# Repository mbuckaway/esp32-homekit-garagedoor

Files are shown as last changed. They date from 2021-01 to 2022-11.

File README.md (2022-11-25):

# ESP32 GarageDoor Controller for HomeKit

## What is it

ESP32 dedicated Garage Door controller. When Espressif, created their Homekit SDK for the ESP32, the time was ripe to move the garage door controller to a smaller platform. The ESP32 IDF and Homekit SDKs made incorporating homekit functionity into a sample platform easy.

For complete information on the project, please see the WIKI in the github repo: [WIKI](https://github.com/mbuckaway/esp32-homekit-garagedoor/wiki)

## How this Works

This device is based on the Espressif SDK and uses the open source version of the Espressif Homekit SDK. It uses my own network component. This network component uses BluFi to configure WIFI creds and control the device. You will need the Espressif EspBluFi app from the Apple Appstore.

The difference with this controller and others is it uses both a switch on the lower part of the door to sensor it's actually closed and a switch on the upper side of the door to sensor it's actually open. With only a close switch, one can only assume the garage door actually makes it all the way up to be open. The two switches allow us to add a motion sensor service to sensor when the door is in motion. I use that to turn the garage light automatically on when the door moves.

The code configures the following services that make up the garage door accessory:

- Garage Door
- Close Sensor
- Open Sensor
- Motion Sensor (sense when the door is in motion)
- Switch to force the door to move (used for automations to override security "issues")
- Switch to close the door when it is open (and only open). Homekit sometimes loses the door status and this control is required for automation to work reliably.

What is missing from this unit is the obstruction detection. At some point, I may add a eye beam to detect something is in the way, but the old garage door already has that as a safety features, so having your phone notify you of the obstruction seems moot.

The code uses a button library to monitor the door switches and automatically debounces the switches. Additionally, the routine the monitors the open and close switches updates Homekit with the changes in status, so the home app almost instantly. However, Homekit seems to have a bug in it where if you control the door without using the Home App, it loses track of the door status. The code updates the status correctly, but Homekit seems to ignore it. That said, it does correct itself when the door is fully closed.

For my device, I included two LED's connected to the switches through resistors. There is no GPIO for these and they are completely optional. I had issues with the door switches not working. During the winter, ice built up on the bottom of the door, and the close switch needed to be repositioned. Include them if you want, but they are not required.

See the WIKI for information on building the device, the circuit, etc.

## Photos

Below are some of the photos from the device I created.

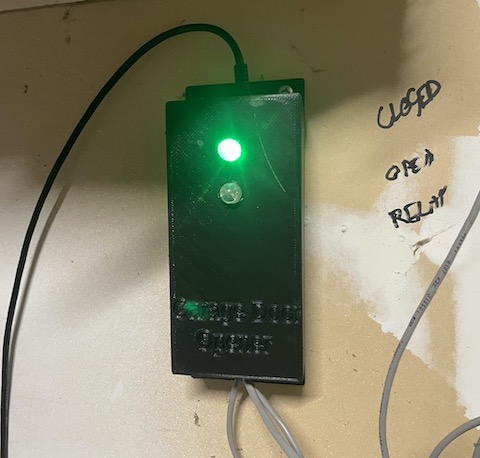
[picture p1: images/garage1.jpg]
Garage Door Controller in 3D Printed Case

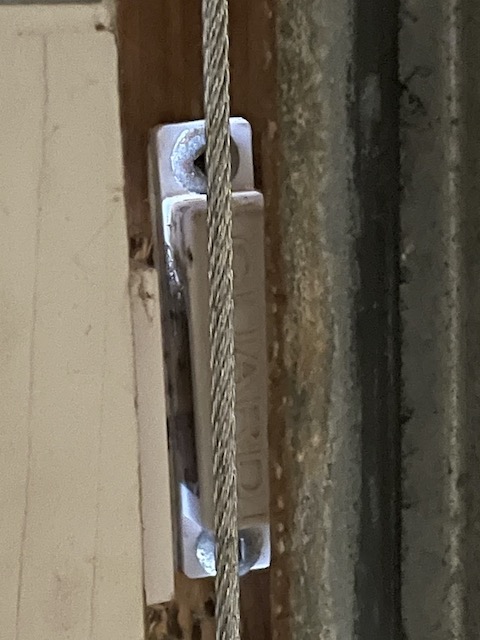
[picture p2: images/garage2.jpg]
Lower magnetic door switch

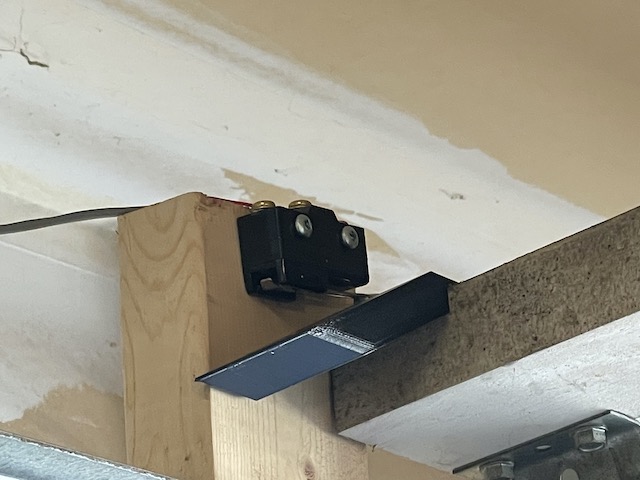
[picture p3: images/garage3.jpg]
Upper roller switch


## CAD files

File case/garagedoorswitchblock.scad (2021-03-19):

$fn = 20;


width = 50;
length = 100;
height = 40;
top_height = 5;

module rounded_box(x,y,z,r){
    translate([r,r,r])
    minkowski(){
        cube([x-r*2,y-r*2,z-r*2]);
        sphere(r=r, $fs=0.1);
    }
}

difference()
{
    rounded_box(length, width, height, 3);
    cube([length/4, width, height-top_height]);
    translate([length-70, 0, height]) rotate([0, 30, 0]) cube([length, width, height+10]);
    translate([length-90, 0, 0]) rotate([0, 30, 0]) cube([length/2+10, width, height-10]);
    translate([15, width/3, 25]) cylinder(h=20, d=5);
    translate([15, width/3*2, 25]) cylinder(h=20, d=5);
    translate([15, width/3, 46]) rotate([180, 0, 0])cylinder(10, 10);
    translate([15, width/3*2, 46]) rotate([180, 0, 0])cylinder(10, 10);
}

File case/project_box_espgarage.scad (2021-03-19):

$fn=50;
//Procedural Project Box Screws

box_enable = 1;
top_enable = 1;
fillets_enable = 1;
fillets2_enable = 1;

text_enable_box = 1;
//40mm x 60 board size

inside_width = 60;
inside_length = 130;
inside_height = 35;
//Wall thickness
thickness = 2.5;                  
//Fillet radius. This should not be larger than thickness.
radius = 2;                     
//Diameter of the holes that screws thread into. 
screw_dia = 2.5;                  
//Diameter of the holes on the lid (should be larger than the diameter of your screws)
screw_loose_dia = 3.2;
//Only use this if the lip on your lid is detached from the lid! This is a hack to work around odd union() behaviour.
extra_lid_thickness = 0;        //Extra lid thickness above thickness. 
                                //You may want to tweak this to account for large chamfer radius.

// The lid can have a lip on it for attached to another surface
// This is the size of that lip
lid_screw_lip_size = 15;
lid_screw_lip_screw_size = 5;
// The side of the box has a hole for the wifi antenna.
// Set to zero to disable.
antenna_holesize=0;
antenna_offset=7;

led_holesize=9.8;
led_offset=25;
led_spacing=20;
led_count = 2;

top_holesize=15;
top_holeoffset = 5;

bottom_holesize=10;

screwmount_height = 12;
screwmount_length = 65;
screwmount_width = 40;
screwmount_offset_x = 12;
screwmount_offset_y = 13;
screwmount_screw_dia = 1.25;

screwmount2_height = 8;
screwmount2_length = 21;
screwmount2_width = 29;
screwmount2_offset_x = 18;
screwmount2_offset_y = 95;


outside_width = inside_width + thickness * 2;
outside_length = inside_length + thickness * 2;
od = screw_dia * 2.5;

module screwmount()
{
    difference() {
        cylinder(r=3.0, h=screwmount_height-2);
        translate([0,0,-1]) cylinder(r=screwmount_screw_dia, h=screwmount_height);
    }
    rotate_extrude(convexity = 10)
        translate([2.5,0,0]) {
            intersection()
            {
                square(5);
                difference() {
                    square(5, center=true);
                    translate([2.5,2,5]) circle(2.0);
                }
            }
        }
}

module filletposts()
{
    postoffset_length = screwmount_length;
    postoffset_width = screwmount_width;
    post1 = [0, 0, 0];
    post2 = [0, postoffset_length, 0];
    post3 = [postoffset_width, 0, 0];
    post4 = [postoffset_width, postoffset_length, 0];
    translate(post1) screwmount();
    translate(post2) screwmount();
    translate(post3) screwmount();
    translate(post4) screwmount();
}

module filletposts2()
{
    postoffset_length = screwmount2_length;
    postoffset_width = screwmount2_width;
    post1 = [0, 0, 0];
    post2 = [0, postoffset_length, 0];
    post3 = [postoffset_width, 0, 0];
    post4 = [postoffset_width, postoffset_length, 0];
    translate(post1) screwmount();
    translate(post2) screwmount();
    translate(post3) screwmount();
    translate(post4) screwmount();
}

module box_screw(id, od, height){
    difference(){
        union(){
            cylinder(d=od, h=height, $fs=0.2);
            translate([-od/2, -od/2, 0])
                cube([od/2,od,height], false);
            translate([-od/2, -od/2, 0])
                cube([od,od/2,height], false);
        }
        cylinder(d=id, h=height, $fn=6);
    }
}

module rounded_box(x,y,z,r){
    translate([r,r,r])
    minkowski(){
        cube([x-r*2,y-r*2,z-r*2]);
        sphere(r=r, $fs=0.1);
    }
}

module main_box(){
    difference(){
        //cube([outside_width, outside_length, inside_height + thickness * 2]);
        difference(){
            rounded_box(outside_width, outside_length, inside_height + thickness + 2, radius);
            translate([0,0,inside_height + thickness])
            cube([outside_width, outside_length, inside_height + thickness * 2]);
        }
        translate([thickness, thickness, thickness])
        cube([inside_width, inside_length, inside_height + thickness]);
        if (antenna_holesize>0)
        {
            translate([thickness/2,inside_length/2,inside_height-antenna_offset]) {
                rotate([0,90,0])
                cylinder(h = thickness*2, d = antenna_holesize, center=true, $fs=0.2);    
            }
        }
        if (led_holesize>0)
        {
            translate([inside_width/2+thickness,led_offset,thickness/2])
                cylinder(h = thickness*2, d = led_holesize+.15, center=true, $fs=0.2);    
            translate([inside_width/2+thickness,led_offset+led_spacing,thickness/2])
                cylinder(h = thickness*2, d = led_holesize, center=true, $fs=0.2);
            if (led_count>2)
            {    
            translate([inside_width/2+thickness,led_offset+led_spacing*2,thickness/2])
                cylinder(h = thickness*2, d = led_holesize, center=true, $fs=0.2);    
            }
            if (led_count>3)
            {
                translate([inside_width/2+thickness,led_offset+led_spacing*3,thickness/2])
                cylinder(h = thickness*2, d = led_holesize, center=true, $fs=0.2);
            }
        }
        if (top_holesize>0)
        {
            translate([inside_width/2+thickness,thickness/2,inside_height/2+thickness+top_holeoffset]) {
                rotate([90,0,0])
                cylinder(h = thickness*2, d = top_holesize, center=true, $fs=0.2);    
            }
        }
        if (bottom_holesize>0)
        {
            translate([inside_width/2+thickness,inside_length+thickness+thickness/2,inside_height/2+thickness]) {
                rotate([90,0,0])
                cylinder(h = thickness*2, d = bottom_holesize, center=true, $fs=0.2);    
            }
        }
        if (text_enable_box)
        {
            translate ([2,inside_length-25,thickness/3]) 
                rotate([180,0,0])
                linear_extrude(thickness/3)
                text("Garage Door", size=8);
            translate ([14,inside_length-10,thickness/3]) 
                rotate([180,0,0])
                linear_extrude(thickness/3)
                text("Opener", size=8);
        }
    }

    od = screw_dia * 2.5;
    
    translate([od/2+thickness,od/2+thickness, 0])
        box_screw(screw_dia, od, inside_height);
    
    translate([thickness+inside_width-od/2, od/2+thickness, 0])
        rotate([0,0,90])
            box_screw(screw_dia, od, inside_height);
    
    translate([thickness+inside_width-od/2, -od/2+thickness+inside_length, 0])
        rotate([0,0,180])
            box_screw(screw_dia, od, inside_height);
    
    translate([od/2 + thickness, -od/2+thickness+inside_length, 0])
        rotate([0,0,270])
            box_screw(screw_dia, od, inside_height);
}

module lid(){
    difference(){
        union(){
        //Lid.
        difference(){
            translate([0,-lid_screw_lip_size,0])
                rounded_box(outside_width, outside_length+lid_screw_lip_size*2, thickness * 4, radius);
            translate([0,-lid_screw_lip_size, thickness + extra_lid_thickness])
                cube([outside_width, outside_length+lid_screw_lip_size*2, inside_height + thickness * 4]);
        }
        //Lip
        lip_tol = 0.5;
        lip_width = inside_width - lip_tol;
        lip_length = inside_length - lip_tol;
        translate([(outside_width - lip_width)/2,(outside_length - lip_length)/2, thickness * 0.99])
            difference(){
                cube([lip_width, lip_length, thickness]);
                translate([thickness, thickness, 0])
                    cube([lip_width-thickness*2, lip_length-thickness*2, thickness]);
        }
        
        intersection(){
            union(){
            translate([od/2 + thickness, od/2 + thickness, thickness])
                box_screw(screw_dia, od, thickness);
            translate([inside_width - od/2 + thickness, od/2 + thickness, thickness])
                rotate([0,0,90])
                    box_screw(screw_dia, od, thickness);
            translate([inside_width - od/2 + thickness, inside_length - od/2 + thickness, thickness])
                rotate([0,0,180])
                    box_screw(screw_dia, od, thickness);
            translate([od/2 + thickness, inside_length - od/2 + thickness, thickness])
                rotate([0,0,270])
                    box_screw(screw_dia, od, thickness);
            }
            translate([thickness + lip_tol, thickness + lip_tol, 0])
            cube([lip_width-lip_tol,lip_length-lip_tol, 200]);
        }
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

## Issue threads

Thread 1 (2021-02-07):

Thank you for your project.

neohusky, 2021-02-07:
Hi Mark

I just stumbled open your project.  I was ready to do a similar project using a pi which I am comfortable with and have now decided to get my feet wet with ESP32.

I’m being lazy here: Any chance you could post a brief wiring diagram for the esp board, relay board and sensors?

mbuckaway, 2021-02-07:
I used a RPi with Homebridge for the project the first time around (my code is on another repo here on Github), but running a full linux distro for something that did this one thing was complete overkill, and I had one of the RPI OS updates completely blow away the SDCARD. The ESP32 does this one thing well, and there is no SDCARD to get damaged - nevermind, it's cheaper. It was a great day be able to pull the RPi off the wall of my garage.

The readme.md really does explain the circuit but perhaps needs a bit of verbosity. II used a ESP32 DevKitC v4 from Aliexpress, but you can buy them anywhere. DigiKey has them if you want it tomorrow. There is one switch mounted at the top of the garage door (door open sensor) and one switch near the bottom of the door (door closed sensor). They are wired directly to the associated GPIO on the ESP32 devkit board. No capacitors or resistors are required because switch debounce is done in software. The switches are active low, so the other side of the switches go to ground on the ESP32. I used a reed switch for the top of the door and a magnetic door close switch for the bottom of the door which I found locally at a hobby electronics shop.

The relay board takes another GPIO  - mine is a 5v relay board, so I wired the 5v line to the 5v line on the ESP32, and ground to the ESP32 ground, and the data line to the ESP32 GPIO. Lots of these are on Alliexpress, but my favourite supply shop locally had them.  The other side of the relay board uses the N/O connections to connect to the garage door switch - so it takes the place of a human. I suggest wiring everything on a breadboard first, and get it working. I used a set of dip switches to similar the door switches for testing.

I power the device from the USB port from a cheap USB power supply which is plugged into the wall in my garage.

Hope that is descriptive enough....I may create a circuit diagram at some point. I updated the code a month ago to make it work correctly - and Siri is quite happy to control my garage door from my HomePod or shut the garage door at 11pm should I leave it open.

Enjoy,
Mark

neohusky, 2021-02-08:
Hey Mark

Thank you for such a detailed explanation of ESP32 circuit. It does seem like a natural evolution from the RPi considering we only require it to do one task.

I’ve ordered my board and look forward to putting this together over the coming weeks.

Thanks Heaps,
Theo

neohusky, 2021-03-16:
G'DAy Mark

I hope you've been safe and well. My components are tricking in.  The only thing I'm missing are the reed switches for the open close sensors.  In any case I've got a testbed and have everything wired and homekit sees my set up.

My question is why would the relay stay permanently energised rather than pulse when I try and open the door using homekit.  I have not yet tried the NO connections yet, but, every time I plug in the data line to the relay I hear it tick and stay engaged (the green light stays permanently on whilst the data line is connected.

Do you have any suggestions on how to troubleshoot this unexpected behaviour?
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

mbuckaway, 2021-03-16:
I suggestion:
- verify that the setup is correct in the idf menuconfig - set the relay GPIO to the one you use. Unconfigured pins on the ESP32 can have an undefined response
- Use the serial monitor to see what is happen on the ESP32 console
- Use a LED (with say a 100 ohm resistor in series) in place of the relay connected to ground.
- If all else fails, create a simple program that does nothing more than toggle a GPIO - you can hard code everything. There is a GPIO example in the ESP-IDF code you can base it on.

Something to consider is the GPIO's on the ESP32 are 3.3v and have a max output of 40ma. If the relay is expecting 5v logic, it might not work correctly. If the LED works and the relay does not, you'll need to find one that supports a 3.3v input. You can also try driving the relay from the 3.3 power supply if it supports it.

Hope that helps.

neohusky, 2021-03-16:
Hey Mark

Thanks for the quick response.  I'm using the standard config of GPIOs and the monitor output is below.

I was going to go back to basics and just do a single button project for testing the relay as you suggested, but, thought there might be something else I've missed.

BTW..I tried the 3.3V input with the same response on the relay.
`I (13555) GDGPIO: Door status check: open=contact not detected - close=contact detected
I (13565) GDGPIO: Reporting door: closed
I (13565) GDGPIO: Kicking the relay...
I (13605) BUTTON: 25 LONG
I (13655) BUTTON: 25 LONG
I (13705) BUTTON: 25 LONG
I (13755) BUTTON: 25 LONG
I (13805) BUTTON: 25 LONG
I (13855) BUTTON: 25 LONG
I (13905) BUTTON: 25 LONG
I (13955) BUTTON: 25 LONG`

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

Closed 2021-02-08.

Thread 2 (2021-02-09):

Submodules not downloading

neohusky, 2021-02-09:
Hey Mark

I've got my board.  I'm just trying to grab your repo and I've run into some issues getting the complete package with the submodules by doing a git clone.  I've also tried to do a recursive clone.  Below is the error.  I'm not sure if its a permissions issue with your repo or misconfiguration on my end.

I'll download the other repo's/sub modules manually in the meantime.

```
Submodule 'components/esp-homekit-sdk' (git@github.com:espressif/esp-homekit-sdk.git) registered for path 'components/esp-homekit-sdk'
Submodule 'components/esp32-button' (git@github.com:craftmetrics/esp32-button.git) registered for path 'components/esp32-button'
Submodule 'components/wifi' (git@github.com:mbuckaway/esp32-wifi-component.git) registered for path 'components/wifi'
Cloning into '/Users/theokitsos/esp/esp32-homekit-garagedoor/components/esp-homekit-sdk'...
git@github.com: Permission denied (publickey).
fatal: Could not read from remote repository.

Please make sure you have the correct access rights
and the repository exists.
fatal: clone of 'git@github.com:espressif/esp-homekit-sdk.git' into submodule path '/Users/theokitsos/esp/esp32-homekit-garagedoor/components/esp-homekit-sdk' failed
```

neohusky, 2021-02-09:
I followed the instructions in your wifi submodule on adding the git repo manually and did the same with the other submodules.  So far so good.

Closed 2021-02-09.

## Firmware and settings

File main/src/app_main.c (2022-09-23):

/*
 * Copyright (c) 2020 <Mark Buckaway> MIT License
 * 
 * HomeKit GarageDoor Project
 */

#include <stdio.h>
#include <string.h>
#include <stdlib.h>
#include <freertos/FreeRTOS.h>
#include <freertos/task.h>
#include "freertos/queue.h"
#include <esp_event.h>
#include <esp_log.h>

#include <hap.h>
#include <hap_apple_servs.h>
#include <hap_apple_chars.h>

//#include <hap_fw_upgrade.h>
//#include <iot_button.h>

#include "network.h"
#include <app_hap_setup_payload.h>

#include "garagedoor.h"
#include "homekit_states.h"

/*  Required for server verification during OTA, PEM format as string  */
char server_cert[] = {};

static const char *TAG = "HAP";

static const uint16_t GARAGEDOOR_TASK_PRIORITY = 5;
static const uint16_t GARAGEDOOR_TASK_STACKSIZE = 4 * 1024;
static const char *GARAGEDOOR_TASK_NAME = "hap_garage";

/* Reset network credentials if button is pressed for more than 3 seconds and then released */
//static const uint16_t RESET_NETWORK_BUTTON_TIMEOUT = 3;

/* Reset to factory if button is pressed and held for more than 10 seconds */
// static const uint16_t RESET_TO_FACTORY_BUTTON_TIMEOUT = 10;

/* The button "Boot" will be used as the Reset button for the example */
//static const uint16_t RESET_GPIO = GPIO_NUM_0;

/* Char definitions for our switches */
static hap_char_t *open_contact_char = 0;
static hap_char_t *close_contact_char = 0;
static hap_char_t *motion_sensor_char = 0;
static hap_char_t *door_switch_char = 0;
static hap_char_t *closeif_door_switch_char = 0;
static hap_char_t *garage_door_current_status_char = 0;
static bool reset_requested = false;

/**
 * @brief The factory reset button callback handler.
 */
void reset_to_factory_handler(void)
{
    // Only allow the routine to be called once. It reboots the device so we start over.
    if (!reset_requested)
    {
        hap_reset_to_factory();
        reset_requested = true;
    }
}

static void reset_network_handler(void)
{
    hap_reset_network();
}

static void reboot_system(void) 
{
    esp_restart();
}

/**
 * Accessory Identity routine. Does nothing other than long the event because the device has no
 * LED to let the user know who we are.
 */
static int garage_identify(hap_acc_t *ha)
{
    ESP_LOGI(TAG, "Garage Door Accessory identified");
    return HAP_SUCCESS;
}

/**
 * Event handler to report what HAP is doing. Useful for debugging.
 */
static void garage_hap_event_handler(void* arg, esp_event_base_t event_base, int32_t event, void *data)
{
    switch(event) {
        case HAP_EVENT_PAIRING_STARTED :
            ESP_LOGI(TAG, "Pairing Started");
            break;
        case HAP_EVENT_PAIRING_ABORTED :
            ESP_LOGI(TAG, "Pairing Aborted");
            break;
        case HAP_EVENT_CTRL_PAIRED :
            ESP_LOGI(TAG, "Controller %s Paired. Controller count: %d",
                        (char *)data, hap_get_paired_controller_count());
            break;
        case HAP_EVENT_CTRL_UNPAIRED :
            ESP_LOGI(TAG, "Controller %s Removed. Controller count: %d",
                        (char *)data, hap_get_paired_controller_count());
            break;
        case HAP_EVENT_CTRL_CONNECTED :
            ESP_LOGI(TAG, "Controller %s Connected", (char *)data);
            break;
        case HAP_EVENT_CTRL_DISCONNECTED :
            ESP_LOGI(TAG, "Controller %s Disconnected", (char *)data);
            break;
        case HAP_EVENT_ACC_REBOOTING : {
            char *reason = (char *)data;
            ESP_LOGI(TAG, "Accessory Rebooting (Reason: %s)",  reason ? reason : "null");
            break;
        }
        default:
            /* Silently ignore unknown events */
            break;
    }
}

/**
 * @brief Update the door status from our door switches
 */
void door_status_update(int state)
{
        hap_val_t new_val;
        new_val.i = state;
        hap_char_update_val(garage_door_current_status_char, &new_val);
}

/* 
 * @brief Check the current status of the garage door and return it to homekit
 */
static int garagedoor_read(hap_char_t *hc, hap_status_t *status_code, void *serv_priv, void *read_priv)
{
    if (hap_req_get_ctrl_id(read_priv)) {
        ESP_LOGI(TAG, "garagedoor received read from %s", hap_req_get_ctrl_id(read_priv));
    }
    if (!strcmp(hap_char_get_type_uuid(hc), HAP_CHAR_UUID_CURRENT_DOOR_STATE)) 
    {
        hap_val_t new_val;
        new_val.i = get_door_current_state();
        hap_char_update_val(hc, &new_val);
        *status_code = HAP_STATUS_SUCCESS;
        ESP_LOGI(TAG,"garagedoor status updated to %s", garagedoor_current_state_string(new_val.i));
    }
    return HAP_SUCCESS;
}

/**
 * @brief Open the garage door when homekit asks for it.
 */
static int garagedoor_write(hap_write_data_t write_data[], int count,
        void *serv_priv, void *write_priv)
{
    if (hap_req_get_ctrl_id(write_priv)) {
        ESP_LOGI(TAG, "garagedoor received write from %s", hap_req_get_ctrl_id(write_priv));
    }
    ESP_LOGI(TAG, "garagedoor write called with %d chars", count);
    int i, ret = HAP_SUCCESS;
    hap_write_data_t *write;
    for (i = 0; i < count; i++) {
        write = &write_data[i];
        if (!strcmp(hap_char_get_type_uuid(write->hc), HAP_CHAR_UUID_TARGET_DOOR_STATE)) {
            ESP_LOGI(TAG, "garagedoor received write TargetDoorState: %s", garagedoor_target_state_string(write->val.b));
            set_door_target_state(write->val.b);
            hap_char_update_val(write->hc, &(write->val));
            *(write->status) = HAP_STATUS_SUCCESS;
        } else {
            *(write->status) = HAP_STATUS_RES_ABSENT;
        }
    }
    return ret;
}

/**
 * @brief Update our door and closeif switches status from the door switches
 */
void door_switches_update(bool state)
{
        hap_val_t new_val;
        new_val.b = state;
        hap_char_update_val(door_switch_char, &new_val);
        hap_char_update_val(closeif_door_switch_char, &new_val);
}

/**
 * @brief Reads the status of the garage door to select if the switch should be on or off. We set it to ON
 * if the door it open, and off if its anything else. Used for the door_switch_service and closeif_switch_service.
 */
static int door_switch_read(hap_char_t *hc, hap_status_t *status_code, void *serv_priv, void *read_priv)
{
    if (hap_req_get_ctrl_id(read_priv)) {
        ESP_LOGI(TAG, "closeif/door_switch received read from %s", hap_req_get_ctrl_id(read_priv));
    }
    if (!strcmp(hap_char_get_type_uuid(hc), HAP_CHAR_UUID_ON)) 
    {
        hap_val_t new_val;
        // use open as on
        new_val.b = (get_door_current_state()==CURRENT_STATE_OPEN);
        hap_char_update_val(hc, &new_val);
        *status_code = HAP_STATUS_SUCCESS;
        ESP_LOGI(TAG,"closeif/door_switch status updated to %s", (new_val.b)?"on(open)":"off(closed)");
    }
    return HAP_SUCCESS;
}

/**
 * @brief Takes a request from homekit and sets the switch status. We use on for open and off for closed
 */
static int door_switch_write(hap_write_data_t write_data[], int count, void *serv_priv, void *write_priv)
{
    if (hap_req_get_ctrl_id(write_priv)) {
        ESP_LOGI(TAG, "door switch received write from %s", hap_req_get_ctrl_id(write_priv));
    }
    ESP_LOGI(TAG, "door switch write called with %d chars", count);
    int i, ret = HAP_SUCCESS;
    hap_write_data_t *write;
    for (i = 0; i < count; i++) {
        write = &write_data[i];
        if (!strcmp(hap_char_get_type_uuid(write->hc), HAP_CHAR_UUID_ON)) {
            ESP_LOGI(TAG, "door switch received write On State: %s", write->val.b?"on(open)":"off(closed)");
            set_door_target_state(write->val.b?TARGET_STATE_OPEN:TARGET_STATE_CLOSED);
            hap_char_update_val(write->hc, &(write->val));
            *(write->status) = HAP_STATUS_SUCCESS;
        } else {
            *(write->status) = HAP_STATUS_RES_ABSENT;
        }
    }
    return ret;
}

/**
 * @brief Takes a request from homekit and sets the switch status. We use on for open and off for closed
 */
static int closeif_switch_write(hap_write_data_t write_data[], int count, void *serv_priv, void *write_priv)
{
    if (hap_req_get_ctrl_id(write_priv)) {
        ESP_LOGI(TAG, "closeif received write from %s", hap_req_get_ctrl_id(write_priv));
    }
    ESP_LOGI(TAG, "closeif write called with %d chars", count);
    int i, ret = HAP_SUCCESS;
    hap_write_data_t *write;
    for (i = 0; i < count; i++) {
        write = &write_data[i];
        if (!strcmp(hap_char_get_type_uuid(write->hc), HAP_CHAR_UUID_ON)) {
            ESP_LOGI(TAG, "closeif received write ON State: %s", write->val.b?"on(open)":"off(closed)");
            force_door_target_state(write->val.b?TARGET_STATE_OPEN:TARGET_STATE_CLOSED);
            hap_char_update_val(write->hc, &(write->val));
            *(write->status) = HAP_STATUS_SUCCESS;
        } else {
            *(write->status) = HAP_STATUS_RES_ABSENT;
        }
    }
    return ret;
}

void open_sensor_update(uint8_t state)
{
        hap_val_t new_val;
        new_val.i = state;
        hap_char_update_val(open_contact_char, &new_val);
}

static int open_sensor_read(hap_char_t *hc, hap_status_t *status_code, void *serv_priv, void *read_priv)
{
    if (hap_req_get_ctrl_id(read_priv)) {
        ESP_LOGI(TAG, "open sensor received read from %s", hap_req_get_ctrl_id(read_priv));
    }
    if (!strcmp(hap_char_get_type_uuid(hc), HAP_CHAR_UUID_CONTACT_SENSOR_STATE)) 
    {
        hap_val_t new_val;
        // use open as on
        new_val.i = get_open_contact_status();
        hap_char_update_val(hc, &new_val);
        *status_code = HAP_STATUS_SUCCESS;
        ESP_LOGI(TAG,"open sensor status updated to %s", contact_state_string(new_val.i));
    }
    return HAP_SUCCESS;
}

void close_sensor_update(uint8_t state)
{
        hap_val_t new_val;
        new_val.i = state;
        hap_char_update_val(close_contact_char, &new_val);
}

static int close_sensor_read(hap_char_t *hc, hap_status_t *status_code, void *serv_priv, void *read_priv)
{
    if (hap_req_get_ctrl_id(read_priv)) {
        ESP_LOGI(TAG, "close sensor received read from %s", hap_req_get_ctrl_id(read_priv));
    }
    if (!strcmp(hap_char_get_type_uuid(hc), HAP_CHAR_UUID_CONTACT_SENSOR_STATE)) 
    {
        hap_val_t new_val;
        // use open as on
        new_val.i = get_close_contact_status();
        hap_char_update_val(hc, &new_val);
        *status_code = HAP_STATUS_SUCCESS;
        ESP_LOGI(TAG,"close sensor status updated to %s", contact_state_string(new_val.i));
    }
    return HAP_SUCCESS;
}

void motion_sensor_update(bool state)
{
        hap_val_t new_val;
        new_val.b = state;
        hap_char_update_val(motion_sensor_char, &new_val);
}

static int motion_sensor_read(hap_char_t *hc, hap_status_t *status_code, void *serv_priv, void *read_priv)
{
    if (hap_req_get_ctrl_id(read_priv)) {
        ESP_LOGI(TAG, "close sensor received read from %s", hap_req_get_ctrl_id(read_priv));
    }
    if (!strcmp(hap_char_get_type_uuid(hc), HAP_CHAR_UUID_MOTION_DETECTED)) 
    {
        hap_val_t new_val;
        // use open as on
        new_val.b = get_motion_detected();
        hap_char_update_val(hc, &new_val);
        *status_code = HAP_STATUS_SUCCESS;
        ESP_LOGI(TAG,"motion sensor status updated to %s", new_val.b?"inmotion":"nomotion");
    }
    return HAP_SUCCESS;
}

/**
 * @brief Main Thread to handle setting up the service and accessories for the GarageDoor
 */
static void garage_thread_entry(void *p)
{
    hap_acc_t *garageaccessory = NULL;
    hap_serv_t *garagedoorservice = NULL;
    hap_serv_t *closeif_switch_service = NULL;
    hap_serv_t *door_switch_service = NULL;
    hap_serv_t *opencontact_sensor_service = NULL;
    hap_serv_t *closecontact_sensor_service = NULL;
    hap_serv_t *motion_sensor_service = NULL;

    /*
     * Configure the GPIO for the garage door state/relay control
     */
    garagedoor_setup();

    /* Configure HomeKit core to make the Accessory name (and thus the WAC SSID) unique,
     * instead of the default configuration wherein only the WAC SSID is made unique.
     */
    ESP_LOGI(TAG, "configuring HAP");
    hap_cfg_t hap_cfg;
    hap_get_config(&hap_cfg);
    hap_cfg.unique_param = UNIQUE_NAME;
    hap_set_config(&hap_cfg);

    ESP_LOGI(TAG, "initializing HAP");
    /* Initialize the HAP core */
    hap_init(HAP_TRANSPORT_WIFI);

    /* Initialise the mandatory parameters for Accessory which will be added as
     * the mandatory services internally
     */
    hap_acc_cfg_t cfg = {
        .name = "Esp-GarageDoor",
        .manufacturer = "Espressif",
        .model = "EspGarageDoor01",
        .serial_num = "001122334455",
        .fw_rev = "0.9.0",
        .hw_rev =  (char*)esp_get_idf_version(),
        .pv = "1.1.0",
        .identify_routine = garage_identify,
        .cid = HAP_CID_GARAGE_DOOR_OPENER,
    };
    ESP_LOGI(TAG, "Creating garage door accessory...");
    /* Create accessory object */
    garageaccessory = hap_acc_create(&cfg);

    /* Add a dummy Product Data */
    uint8_t product_data[] = {'E','S','P','3','2','H','A','P'};
    hap_acc_add_product_data(garageaccessory, product_data, sizeof(product_data));

    uint8_t currentdoorstate = get_door_current_state();
    
    ESP_LOGI(TAG, "Creating garage door service (current state: %s)", garagedoor_current_state_string(currentdoorstate));

    /* Create the GarageDoor Service. Include the "name" since this is a user visible service  */
    garagedoorservice = hap_serv_garage_door_opener_create(currentdoorstate, TARGET_STATE_CLOSED, false);
    hap_serv_add_char(garagedoorservice, hap_char_name_create("ESP Garage Door"));
    /* Set the write callback for the service */
    hap_serv_set_write_cb(garagedoorservice, garagedoor_write);
    /* Set the read callback for the service (optional) */
    hap_serv_set_read_cb(garagedoorservice, garagedoor_read);
    /* Add the Garage Service to the Accessory Object */
    hap_acc_add_serv(garageaccessory, garagedoorservice);
    garage_door_current_status_char = hap_serv_get_char_by_uuid(garagedoorservice, HAP_CHAR_UUID_CURRENT_DOOR_STATE);

    ESP_LOGI(TAG, "Creating closeif service (current state: %s)", (currentdoorstate==CURRENT_STATE_OPEN)?"on(open)":"off(closed)");
    // Create the CloseIf switch
    closeif_switch_service = hap_serv_switch_create((bool)(currentdoorstate==CURRENT_STATE_OPEN));
    hap_serv_add_char(closeif_switch_service, hap_char_name_create("ESP CloseIf Door"));
    hap_serv_set_read_cb(closeif_switch_service, door_switch_read);
    hap_serv_set_write_cb(closeif_switch_service, closeif_switch_write);
    hap_acc_add_serv(garageaccessory, closeif_switch_service);
    closeif_door_switch_char = hap_serv_get_char_by_uuid(closeif_switch_service, HAP_CHAR_UUID_ON);

    ESP_LOGI(TAG, "Creating door switch service (current state: %s)", (currentdoorstate==CURRENT_STATE_OPEN)?"on(open)":"off(closed)");
    // Create the CloseIf switch
    door_switch_service = hap_serv_switch_create((bool)(currentdoorstate==CURRENT_STATE_OPEN));
    hap_serv_add_char(door_switch_service, hap_char_name_create("ESP Door Switch"));
    hap_serv_set_read_cb(door_switch_service, door_switch_read);
    hap_serv_set_write_cb(door_switch_service, door_switch_write);
    hap_acc_add_serv(garageaccessory, door_switch_service);
    door_switch_char = hap_serv_get_char_by_uuid(door_switch_service, HAP_CHAR_UUID_ON);

    // Create the open contact sensor
    uint8_t openstate = get_open_contact_status();
    ESP_LOGI(TAG, "Creating open contact service (current state: %s)", contact_state_string(openstate));
    opencontact_sensor_service = hap_serv_contact_sensor_create(openstate);
    hap_serv_add_char(opencontact_sensor_service, hap_char_name_create("ESP Open Contact Sensor"));
    hap_serv_set_read_cb(opencontact_sensor_service, open_sensor_read);
    hap_acc_add_serv(garageaccessory, opencontact_sensor_service);
    open_contact_char = hap_serv_get_char_by_uuid(opencontact_sensor_service, HAP_CHAR_UUID_CONTACT_SENSOR_STATE);

    // Create the open contact sensor
    uint8_t closestate = get_open_contact_status();
    ESP_LOGI(TAG, "Creating close contact service (current state: %s)", contact_state_string(closestate));
    closecontact_sensor_service = hap_serv_contact_sensor_create(get_close_contact_status());
    hap_serv_add_char(closecontact_sensor_service, hap_char_name_create("ESP Close Contact Sensor"));
    hap_serv_set_read_cb(closecontact_sensor_service, close_sensor_read);
    hap_acc_add_serv(garageaccessory, closecontact_sensor_service);
    close_contact_char = hap_serv_get_char_by_uuid(closecontact_sensor_service, HAP_CHAR_UUID_CONTACT_SENSOR_STATE);

    bool inmotion = get_motion_detected();
    ESP_LOGI(TAG, "Creating motion service (current state: %s)", inmotion?"inmotion":"nomotion");
    motion_sensor_service = hap_serv_motion_sensor_create(inmotion);
    hap_serv_add_char(motion_sensor_service, hap_char_name_create("ESP Garage Motion Sensor"));
    hap_serv_set_read_cb(motion_sensor_service, motion_sensor_read);
    hap_acc_add_serv(garageaccessory, motion_sensor_service);
    motion_sensor_char = hap_serv_get_char_by_uuid(motion_sensor_service, HAP_CHAR_UUID_MOTION_DETECTED);


#if 0
    /* Create the Firmware Upgrade HomeKit Custom Service.
     * Please refer the FW Upgrade documentation under components/homekit/extras/include/hap_fw_upgrade.h
     * and the top level README for more information.
     */
    hap_fw_upgrade_config_t ota_config = {
        .server_cert_pem = server_cert,
    };
    service = hap_serv_fw_upgrade_create(&ota_config);
    /* Add the service to the Accessory Object */
    hap_acc_add_serv(accessory, service);
#endif

    /* Add the Accessory to the HomeKit Database */
    ESP_LOGI(TAG, "Adding Garage Door Accessory...");
    hap_add_accessory(garageaccessory);

    /* Register a common button for reset Wi-Fi network and reset to factory.
     */
//    ESP_LOGI(TAG, "Register reset GPIO (reset button) on pin %d", RESET_GPIO);
//    reset_key_init(RESET_GPIO);

    /* Register an event handler for HomeKit specific events */
    esp_event_handler_register(HAP_EVENT, ESP_EVENT_ANY_ID, &garage_hap_event_handler, NULL);

    /* Query the controller count (just for information) */
    ESP_LOGI(TAG, "Accessory is paired with %d controllers", hap_get_paired_controller_count());


    /* For production accessories, the setup code shouldn't be programmed on to
     * the device. Instead, the setup info, derived from the setup code must
     * be used. Use the factory_nvs_gen utility to generate this data and then
     * flash it into the factory NVS partition.
     *
     * By default, the setup ID and setup info will be read from the factory_nvs
     * Flash partition and so, is not required to set here explicitly.
     *
     * However, for testing purpose, this can be overridden by using hap_set_setup_code()
     * and hap_set_setup_id() APIs, as has been done here.
     * 
     * That said, this garage door controller is meant for home use, and not for production,
     * so it it OK to hard code the device info.
     */
#ifdef CONFIG_HOMEKIT_USE_HARDCODED_SETUP_CODE
    /* Unique Setup code of the format xxx-xx-xxx. Default: 111-22-333 */
    hap_set_setup_code(CONFIG_HOMEKIT_SETUP_CODE);
    /* Unique four character Setup Id. Default: ES32 */
    hap_set_setup_id(CONFIG_HOMEKIT_SETUP_ID);
#ifdef CONFIG_APP_WIFI_USE_WAC_PROVISIONING
    app_hap_setup_payload(CONFIG_HOMEKIT_SETUP_CODE, CONFIG_HOMEKIT_SETUP_ID, true, cfg.cid);
#else
    app_hap_setup_payload(CONFIG_HOMEKIT_SETUP_CODE, CONFIG_HOMEKIT_SETUP_ID, false, cfg.cid);
#endif
#endif

    /* mfi is not supported */
    hap_enable_mfi_auth(HAP_MFI_AUTH_NONE);

    ESP_LOGI(TAG, "Starting WIFI...");
    /* Initialize Wi-Fi */
    network_setup();

    start_garagedoor();

    network_waitforconnect();


    /* After all the initializations are done, start the HAP core */
    ESP_LOGI(TAG, "Starting HAP...");
    hap_start();
    
    ESP_LOGI(TAG, "HAP initialization complete.");

    /* The task ends here. The read/write callbacks will be invoked by the HAP Framework */
    vTaskDelete(NULL);
}

#ifdef CONFIG_ESP_BLUFI_ENABLED
/**
 * Define our commands to use for the blufi custom data
 */
#define NUMCMDS 3
static bluficmd_t blufi_commands[NUMCMDS] = {
    { "reboot", &reboot_system },
    { "habreset", &reset_to_factory_handler },
    { "netreset", &reset_network_handler },
};

void process_custom_cmd(const char* data)
{
    ESP_LOGI(TAG, "Received command: %s", data);
    for(int i=0; i < NUMCMDS; i++)
    {
        ESP_LOGI(TAG, "Found cmd: %s", blufi_commands[i].command);
        if (strcmp(blufi_commands[i].command, data) == 0)
        {
            ESP_LOGI(TAG, "Running command: %s", blufi_commands[i].command);
            blufi_commands[i].cmd_callback();
            break;
        }
    }
}
#endif

void app_main()
{
    ESP_LOGI(TAG, "[APP] Startup...");
    ESP_LOGI(TAG, "[APP] Free memory: %d bytes", esp_get_free_heap_size());
    ESP_LOGI(TAG, "[APP] IDF version: %s", esp_get_idf_version());

    esp_log_level_set("*", ESP_LOG_INFO);
    esp_log_level_set("TRANSPORT_TCP", ESP_LOG_VERBOSE);
    esp_log_level_set("TRANSPORT_SSL", ESP_LOG_VERBOSE);
    esp_log_level_set("TRANSPORT", ESP_LOG_VERBOSE);
    esp_log_level_set("OUTBOX", ESP_LOG_VERBOSE);

#ifdef CONFIG_ESP_BLUFI_ENABLED
    void (*ptr_callback)(const char*) = &process_custom_cmd;
    set_custom_command_callback(ptr_callback);
#endif

    ESP_LOGI(TAG, "[APP] Creating main thread...");

    xTaskCreate(garage_thread_entry, GARAGEDOOR_TASK_NAME, GARAGEDOOR_TASK_STACKSIZE, NULL, GARAGEDOOR_TASK_PRIORITY, NULL);
}

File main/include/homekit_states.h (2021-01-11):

#pragma once

#include <stdlib.h>

/**
 * TargetDoorState enum - matches homekit status for same
    Characteristic.TargetDoorState.OPEN = 0;
    Characteristic.TargetDoorState.CLOSED = 1;
 */
enum TargetDoorState {
    TARGET_STATE_OPEN = 0,
    TARGET_STATE_CLOSED = 1
};

/**
 * CurrentDoorState enum - matches homekit status for same
    Characteristic.CurrentDoorState.OPEN = 0;
    Characteristic.CurrentDoorState.CLOSED = 1;
    Characteristic.CurrentDoorState.OPENING = 2;
    Characteristic.CurrentDoorState.CLOSING = 3;
    Characteristic.CurrentDoorState.STOPPED = 4;
 */
enum CurrentDoorState {
    CURRENT_STATE_OPEN = 0,
    CURRENT_STATE_CLOSED = 1,
    CURRENT_STATE_OPENING = 2,
    CURRENT_STATE_CLOSING = 3,
    CURRENT_STATE_STOPPED = 4
};

/**
 * ContactState enum - matches the homekit status for same
 * Characteristic.ContactSensorState.CONTACT_DETECTED = 0;
 * Characteristic.ContactSensorState.CONTACT_NOT_DETECTED = 1;
 */
enum ContactState {
    CONTACT_DETECTED = 0,
    CONTACT_NOT_DETECTED = 1
};

char *garagedoor_current_state_string(uint8_t state);
char *garagedoor_target_state_string(uint8_t state);
char *contact_state_string(uint8_t state);

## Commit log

2020-10-21 Code for sensors.
2020-11-02 Door switch and code cleanup
2020-11-03 readme and motion sensor added
2021-01-01 Fixed sensor bugs
2021-01-11 Added button lib, status updates on changes
2021-03-19 Added better readme
    [garagedoorswitchblock.scad, project_box_espgarage.scad]
2022-09-21 Added reboot, etc. commands for blufi custom data
    [app_main.c]
